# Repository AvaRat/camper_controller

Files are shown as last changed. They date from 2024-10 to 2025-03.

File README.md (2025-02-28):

# Camper Controller

## Overview
The project aims to create a usable system that can be mounted in a campervan, trailer, 4x4 overland vehicle or even small boat. It might be usefull in setups where 12V installation is present.
High level system design is presented in [system design doc](<CamperVan Control Unit system design.pdf>) .

## How to interpret this repo
Project contains electronic parts as well as control logic and user interface source codes. I decided to keep everything in one repo as all parts are pretty much dependent on each other, and with this being one-person project keeping all parts in one place make perfect sense to me.

Please see [design decisions.md](design_decisions.md) for details regarding some of the decision made.

## Roadmap
One of the gratest inspirations for me regarding how to organise things is the Opulo project: [opulo](https://github.com/opulo-inc/lumenpnp/tree/main) I'm still far away from it, but that's something I'm aiming for with respect to project structure and organisation.

Ideally I would like to use github pipelines to create BOM from PCB design files. Also somehow linking pin assignment from Kicad into C code would be great. 

Besides, the project is still in the early phase and requires some time to bring it to working prototype phase.

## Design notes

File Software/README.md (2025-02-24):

# Software for Camper Controller

UI is currently written in pure C while Control unit is done with a mix of C and C++.  This might be unified in the future.

# Overview
This part is split into [an UI part](Software/touch_screen_ui)
and [central  control unit](Software/central_control_unit).

## UI
UI is written using LVGL framework. Currently an app for 7-inch screen was done. See [an actual app](Software/touch_screen_ui/7-inch-lcd-esp32-s3/main/main.c) for more details.
Also vs-code simulator was made to allow for quick prototyping without uploading code to MCU. [a simulator](Software/touch_screen_ui/lv_port_pc_vscode)

## Central Control Unit (CCU)

Main module which will serve as a source of information to the UI. Module will communicate using CAN. This part is under heavy development currently, but some components were already done like: high-side-switch porting [hss-esp.cpp](Software/central_control_unit/components/high_side_switch/hss-esp.cpp)

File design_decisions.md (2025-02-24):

# Design Decisions

## 12V Load Switching and protection

A couple of options are available that are widely used in automotive electronics:
1. physical buttons with thermal fuses
2. relays with thermal fuses
3. semiconductor based switches with  built-in protection

My first design bas based on relays with thermal fuses. It's pretty easy to do and components are widely available. This would probably by the go-to solution for most. However after doing some research I discovered that a recent trend in automotive electronics is to utilize silicon-based switching with protection. Not only it allows to have more control but also the size of a whole device can be decreased. Additionally a module with a built in protection can be "hidden" deeply and no access for fuse replacement is required. 
I decided to try the silicon-based switching eventually. BTS700x family of switches from Infineon were used as they provide a C++ library to control them which makes a development much faster. [high-side-switch repo](https://github.com/Infineon/high-side-switch)

## MCU for Control Unit
ESP32 platform was chosen becouse of my past experience with it. I experimented with RP-Pico for some time, but with much broader, ready to use component library available for ESP-IDF platform development will be much faster. Price is comparable between those two. 

## Lightning
Initially standard 12V LED strip was planned. However with addressable LED strips like those based on WS2812b chip there are much more possibilities for amazing lightning effects, color changes and more. This is my current approach. It's realised using RMT module in ESP.

## Water Sensor
A simple sensor based on 4 metal probes is perfectly enough. This was already tested and solution based on comparator circuit (like LM393) works great.

## User Interface
Initially I wanted to do some user interface on linux OS with a SBC like RPI zero. This hovewer will increase the cost of a whole system rather significantly ($20 for a just a board without display) and the energy usage. Currently I'm exploring aa ESP32-S3 based display module like this one [crowpanel 7inch](https://www.elecrow.com/crowpanel-advance-7-0-hmi-esp32-ai-display-800x480-artificial-intelligent-ips-touch-screen-support-meshtastic-and-arduino-lvgl-micropython.ht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)
The cost for a whole module is $20-$30 which is great. Simple UI app was created for such module and you can find it here [7_inch lcd LVGL app](Software/touch_screen_ui/7-inch-lcd-esp32-s3/main/main.c)

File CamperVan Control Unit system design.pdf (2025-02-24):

# CamperVan Control Unit system design

## Introduction

While building my own van I came across multiple challenges in both domains technical and logistics. Off couse the main issue was the cost of the components that I wanted to purchase ;) That's why I started to build my own parts for it. I graduated robotics with a strong software focus, so the obvious direction for me was to develop my own control board. There are a couple of off the shelf options, but none of them suit me well.
Also designing a product from scratch that I see a specific use case for is fun.

First let's discuss market available options:
1. https://cbe.it/en/Standard-products/New-technology/Control-panels
2. https://simarine.net/via/
3. https://www.garmin.com/en-US/p/716468
4. https://www.garmin.com/en-US/p/861146/pn/010-02764-00
5. https://www.garmin.com/en-US/c/marine/digital-switching/
The rough price for such a system (central unit and display) can be between 200 and 1000 euro, so I have some room to play with.

## The main functions I want to implement and I believe are important for the end user:

1. Enable user to switch power for multiple loads
2. Provide safety for 12V power distribution system
3. Enable user to control the system from multiple places (front and rear of the van, smartphone)
4. Grid connection detection so the system can change behaviour when there's free power from the grid.
5. Provide intelligent lightning control (change of brightness, ideally color for mood-based scenarios)
6. Monitor core parameters like:
6.1. temperature outside
6.2. temperature inside
6.3. Main Battery State of Charge
6.4. Water left in main tank
6.5. Grey water tank status (if full)

Other, more generic parameters that are important:

- Ease of Use for the user
- Ease of installation
- Low price
- Small size
- Low power consumptions

## System Design

Now based on the identified requirements let’s discuss specific features and components of the system.

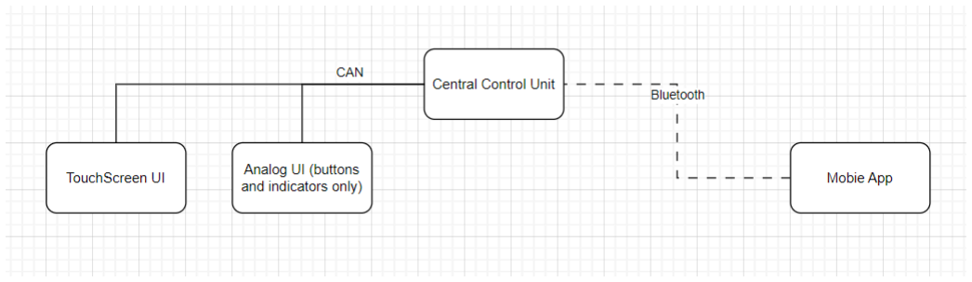
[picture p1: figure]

1. Central Control Unit

This will be the main part. All high-power connections as well as smaller loads and sensors should connect to it.This part can be mounted in inaccessible places, so another device for user interaction is required.

2. TouchScreen User Interface

Digital LCD based panel gives the most flexibility, but also requires the most work.

3. Analog User Interface

This option for user interface is the easiest to implement, so will be the cheapest. However it’s difficult to allow users to control all the features implemented in the Main Control Unit.This will be the minimal version allowing only to switch loads, display battery level and some binary indicators.

## Implementation

From the implementation perspective there are 3 parts:
1. Software:
a. Embedded development
b. User interface development
c. Mobile App (optionally)
2. Electronics:
a. Main Control Unit PCB design
b. Analog UI PCB design
c. TouchScreen module will be purchased as a ready module
3. Hardware:
a. Simple 3d-printed enclosures
b. Off the shelf buttons

This repo is split in this way too. So please check out the part that interests you the most ;)

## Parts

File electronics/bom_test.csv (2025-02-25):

Reference | Value | Datasheet | Footprint | Qty | DNP | lcsc_part | TME
C1,C3,C13,C16,C22,C23,C24,C26,C28,C29,C30,C31,C32,C33 | C_Polarized | ~ | Capacitor_THT:CP_Radial_D5.0mm_P2.50mm | 14
C2,C4,C14 | C | ~ | Capacitor_SMD:C_0805_2012Metric | 3
C5,C6,C7,C8,C15 | 1uF | ~ | Capacitor_SMD:C_0805_2012Metric | 5
C9 | 4.7uF | ~ | Capacitor_SMD:C_0805_2012Metric | 1
C10 | 22uF | ~ | Capacitor_SMD:C_0805_2012Metric | 1
C11,C12,C27 | 100nF | ~ | Capacitor_SMD:C_0805_2012Metric | 3
C17,C18,C19,C20,C21,C25 | 10uF | ~ | Capacitor_SMD:C_0805_2012Metric | 6
D1,D13,D14 | LED | ~ | LED_SMD:LED_1206_3216Metric | 3
D2 | 1N4148W | https://www.vishay.com/docs/85748/1n4148w.pdf | Diode_SMD:D_SOD-123 | 1
D3,D4,D5,D6,D7,D8,D9,D10,D11,D16,D17,D18,D19,D20,D21 | WS2812B | https://cdn-shop.adafruit.com/datasheets/WS2812B.pdf | LED_SMD:LED_WS2812B_PLCC4_5.0x5.0mm_P3.2mm | 15
D12 | D_Schottky_AKA | https://www.vishay.com/docs/98173/v6pwl45.pdf | Package_TO_SOT_SMD:TO-252-2 | 1
D15 | D_Schottky | ~ | Diode_SMD:D_SMA | 1
D22 | D_Schottky | ~ | Diode_THT:D_DO-15_P3.81mm_Vertical_AnodeUp | 1 | DNP
F1,F2,F3,F4,F5 | 20A | -- mixed values -- | HeavyDuty:ATO_fuse_holder | 5 |  | -- mixed values --
F6 | 5A | ~ | HeavyDuty:ATO_fuse_holder | 1
FB1 | FerriteBead 47 Ohm | ~ | Inductor_SMD:L_Walsin_WLFM201609x | 1
GND_Conn1,J11,U4,U12,U16,U18 | ~ |  | -- mixed values -- | 6
J1 | leds_ch1 | ~ | TerminalBlock:TerminalBlock_Xinya_XY308-2.54-3P_1x03_P2.54mm_Horizontal | 1
J2 | CAN | ~ | TerminalBlock:TerminalBlock_Xinya_XY308-2.54-2P_1x02_P2.54mm_Horizontal | 1
J3,J28 | Conn_01x08 | ~ | TerminalBlock:TerminalBlock_Xinya_XY308-2.54-8P_1x08_P2.54mm_Horizontal | 2
J4,J8,J12,J23,J24 | Conn_01x01 | ~ | HeavyDuty:keystone_m3_screw_terminal_vertical | 5
J5 | DB12 | https://www.lcsc.com/datasheet/lcsc_datasheet_2301061509_DORABO-DB128V-5-08-5P-GN-S_C2927513.pdf | HeavyDuty:5p_terminal_DB12 | 1
J6 | Inverter_Conn | ~ | HeavyDuty:keystone_m3_screw_terminal_vertical | 1
J7 | grey_water_conn | ~ | Connector_Samtec_HPM_THT:Samtec_HPM-02-01-x-S_Straight_1x02_Pitch5.08mm | 1
J9,J10 | water_sensor_conn | ~ | TerminalBlock:TerminalBlock_Xinya_XY308-2.54-5P_1x05_P2.54mm_Horizontal | 2
J13,J21,J22 | Conn_01x02 | ~ | TerminalBlock:TerminalBlock_Xinya_XY308-2.54-2P_1x02_P2.54mm_Horizontal | 3
J14,J25,J29,J30,J31 | Conn_GND | ~ | HeavyDuty:keystone_m3_screw_terminal_vertical | 5
J15 | Battery_Conn | ~ | HeavyDuty:keystone_m3_screw_terminal_vertical | 1
J16 | USB_C_Receptacle_USB2.0_16P | https://www.usb.org/sites/default/files/documents/usb_type-c.zip | Connector_USB:USB_C_Receptacle_JAE_DX07S016JA1R1500 | 1
J17,J18 | Conn_01x03 | ~ | TerminalBlock:TerminalBlock_Xinya_XY308-2.54-3P_1x03_P2.54mm_Horizontal | 2
J19 | Conn_01x03 | ~ | TerminalBlock:TerminalBlock_Xinya_XY308-2.54-3P_1x03_P2.54mm_Horizontal | 1 | DNP
J20 | leds_ch2 | ~ | TerminalBlock:TerminalBlock_Xinya_XY308-2.54-3P_1x03_P2.54mm_Horizontal | 1
J26 | leds_ch3 | ~ | TerminalBlock:TerminalBlock_Xinya_XY308-2.54-3P_1x03_P2.54mm_Horizontal | 1
J27 | leds_ch4 | ~ | TerminalBlock:TerminalBlock_Xinya_XY308-2.54-3P_1x03_P2.54mm_Horizontal | 1
Q1 | Q_NMOS_DGS | ~ | Package_TO_SOT_SMD:SOT-323_SC-70 | 1
Q2,Q3 | Q_PMOS_DGS | ~ | Package_TO_SOT_SMD:SOT-323_SC-70 | 2
Q4 | Q_NMOS_GDS | https://wmsc.lcsc.com/wmsc/upload/file/pdf/v2/lcsc/2310271812_UMW-Youtai-Semiconductor-Co---Ltd--AOD413A-UMW_C19100585.pdf | Package_TO_SOT_SMD:TO-252-2 | 1
R1,R27,R32,R37,R38,R39 | 10k | ~ | Resistor_SMD:R_0805_2012Metric | 6
R2,R36 | 100R | ~ | Resistor_SMD:R_0805_2012Metric | 2
R3,R4,R18,R19,R20,R33,R34,R35 | 4k7 | ~ | Resistor_SMD:R_0805_2012Metric | 8
R5,R8 | 0.001 Ohm 10W | https://www.mouser.pl/datasheet/2/392/Susumu_7_1_2024_MSRSF-3471975.pdf | HeavyDuty:MSRSF_shunt_resistor | 2
R6 | 0.003 Ohm 10W | https://www.mouser.pl/ProductDetail/Susumu/MSRSF5930P-3L00-F2P0?qs=VVKQmw408U%252Bnsh6uhhzxQg%3D%3D | HeavyDuty:MSRSF_shunt_resistor | 1
R7,R9,R10,R11,R12,R13 | 10 ohm | -- mixed values -- | Resistor_SMD:R_0805_2012Metric | 6
R14,R15,R21,R_DEN1,R_DEN2,R_DEN3,R_DEN4,R_DEN5,R_IN1,R_IN2,R_IN3,R_IN4,R_IN5 | 4.7k | -- mixed values -- | Resistor_SMD:R_0805_2012Metric | 13
R16,R23,R24,R26 | 100k | -- mixed values -- | -- mixed values -- | 4
R17 | 120 | ~ | Resistor_SMD:R_0805_2012Metric | 1
R22 | 50 Ohm | ~ | Resistor_SMD:R_0805_2012Metric | 1
R25 | 4.7kΩ | ~ | Resistor_SMD:R_0805_2012Metric | 1
R28,R29,R30,R31 | 1M | ~ | Resistor_SMD:R_0805_2012Metric | 4
RL1 | AZSR131-1AE-12D | https://www.mouser.pl/datasheet/2/1628/pre29-3510988.pdf | HeavyDuty:PRE29-same-sky | 1
SW1,SW2,SW3,SW4,SW5 | SW_Push | ~ | analog_ui:button_12mm | 5
SW6 | SW_DIP_x01 | ~ | Connector_PinHeader_1.00mm:PinHeader_1x02_P1.00mm_Vertical | 1
SW7 | RST_BTN | ~ | Button_Switch_THT:SW_PUSH_6mm_H4.3mm | 1
SW8 | FLASH_BTN | ~ | Button_Switch_THT:SW_PUSH_6mm_H4.3mm | 1
U1 | TLV1117-33 | http://www.ti.com/lit/ds/symlink/tlv1117.pdf | Package_TO_SOT_SMD:SOT-223-3_TabPin2 | 1
U3 | TJA1051T-3 | http://www.nxp.com/docs/en/data-sheet/TJA1051.pdf | Package_SO:SOIC-8_3.9x4.9mm_P1.27mm | 1
U5,U14 | LM339_4ch |  | Package_SO:SOIC-14_3.9x8.7mm_P1.27mm | 2
U6,U7,U8,U9,U10 | BTS7006 | https://www.infineon.com/dgdl/Infineon-BTS7004-1EPP-DS-v01_00-EN.pdf?fileId=5546d4626102d35a016147550a725555 | Package_SO:Infineon_PG-TSDSO-14-22 | 5
U11 | INA3221 | http://www.ti.com/lit/ds/symlink/ina3221.pdf | Package_DFN_QFN:Texas_RGV0016A_VQFN-16-1EP_4x4mm_P0.65mm_EP2.1x2.1mm | 1
U13 | CNY17-1 | http://www.vishay.com/docs/83606/cny17.pdf | Package_TO_SOT_SMD:SOT-23-6 | 1
U15 | TCA9555PWR | http://www.ti.com/lit/ds/symlink/tca9555.pdf | Package_SO:TSSOP-24_4.4x7.8mm_P0.65mm | 1 |  |  | TCA9554APWR
U17 | H11AA1 | https://www.vishay.com/docs/83608/h11aa1.pdf | Package_DIP:DIP-6_W7.62mm | 1
U19 | ESP32-S3-MINI-1 | https://www.espressif.com/sites/default/files/documentation/esp32-s3-mini-1_mini-1u_datasheet_en.pdf | PCM_Espressif:ESP32-S3-MINI-1U | 1

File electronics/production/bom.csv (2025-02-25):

Designator | Footprint | Quantity | Value | LCSC Part #
C1, C13, C16, C22, C23, C24, C26, C28, C29, C3, C30, C31, C32, C33 | CP_Radial_D5.0mm_P2.50mm | 14 | C_Polarized
C10_2, C10 | 0805 | 2 | 22uF
C11, C12, C27 | 0805 | 3 | 100nF
C14, C2, C4 | 0805 | 3 | C
C15, C5, C6, C7, C8 | 0805 | 5 | 1uF
C17, C18, C19, C20, C21, C25 | 0805 | 6 | 10uF
C9 | 0805 | 1 | 4.7uF
D1, D13, D14 | 1206 | 3 | LED
D10, D11, D16, D17, D18, D19, D20, D21, D3, D4, D5, D6, D7, D8, D9 | LED_WS2812B_PLCC4_5.0x5.0mm_P3.2mm | 15 | WS2812B
D12 | TO-252-2 | 1 | D_Schottky_AKA
D15 | D_SMA | 1 | D_Schottky
D2 | D_SOD-123 | 1 | 1N4148W
D22 | D_DO-15_P3.81mm_Vertical_AnodeUp | 1 | D_Schottky
F1, F2, F3, F4, F5 | ATO_fuse_holder | 5 | 20A
F6 | ATO_fuse_holder | 1 | 5A
FB1 | L_Walsin_WLFM201609x | 1 | FerriteBead 47 Ohm
GND_CONN1 | small_busbar-15mm | 1 | ~
J1 | TerminalBlock_Xinya_XY308-2.54-3P_1x03_P2.54mm_Horizontal | 1 | leds_ch1
J10, J9 | TerminalBlock_Xinya_XY308-2.54-5P_1x05_P2.54mm_Horizontal | 2 | water_sensor_conn
J11 | water_sensor_rods | 1 | ~
J12, J23, J24, J4, J8 | keystone_m3_screw_terminal_vertical | 5 | Conn_01x01
J13, J21, J22 | TerminalBlock_Xinya_XY308-2.54-2P_1x02_P2.54mm_Horizontal | 3 | Conn_01x02
J14, J25, J29, J30, J31 | keystone_m3_screw_terminal_vertical | 5 | Conn_GND
J15 | keystone_m3_screw_terminal_vertical | 1 | Battery_Conn
J16 | USB_C_Receptacle_JAE_DX07S016JA1R1500 | 1 | USB_C_Receptacle_USB2.0_16P
J17, J18 | TerminalBlock_Xinya_XY308-2.54-3P_1x03_P2.54mm_Horizontal | 2 | Conn_01x03
J2 | TerminalBlock_Xinya_XY308-2.54-2P_1x02_P2.54mm_Horizontal | 1 | CAN
J20 | TerminalBlock_Xinya_XY308-2.54-3P_1x03_P2.54mm_Horizontal | 1 | leds_ch2
J26 | TerminalBlock_Xinya_XY308-2.54-3P_1x03_P2.54mm_Horizontal | 1 | leds_ch3
J27 | TerminalBlock_Xinya_XY308-2.54-3P_1x03_P2.54mm_Horizontal | 1 | leds_ch4
J28, J3 | TerminalBlock_Xinya_XY308-2.54-8P_1x08_P2.54mm_Horizontal | 2 | Conn_01x08
J5 | 5p_terminal_DB12 | 1 | DB12
J6 | keystone_m3_screw_terminal_vertical | 1 | Inverter_Conn
J7 | Samtec_HPM-02-01-x-S_Straight_1x02_Pitch5.08mm | 1 | grey_water_conn
Q1 | SOT-323_SC-70 | 1 | Q_NMOS_DGS
Q2, Q3 | SOT-323_SC-70 | 2 | Q_PMOS_DGS
Q4 | TO-252-2 | 1 | Q_NMOS_GDS | C19100585
R1, R27, R32, R37, R38, R39 | 0805 | 6 | 10k
R10, R11, R12, R13, R7, R9 | 0805 | 6 | 10 ohm
R14, R15, R21, R_DEN1, R_DEN2, R_DEN3, R_DEN4, R_DEN5, R_IN1, R_IN2, R_IN3, R_IN4, R_IN5 | 0805 | 13 | 4.7k
R16, R26 | 0805 | 2 | 100k
R17 | 0805 | 1 | 120
R18, R19, R20, R3, R33, R34, R35, R4 | 0805 | 8 | 4k7
R2, R36 | 0805 | 2 | 100R
R22 | 0805 | 1 | 50 Ohm
R23, R24 | R_Axial_DIN0207_L6.3mm_D2.5mm_P7.62mm_Horizontal | 2 | 100k
R25 | 0805 | 1 | 4.7kΩ
R28, R29, R30, R31 | 0805 | 4 | 1M
R5, R8 | MSRSF_shunt_resistor | 2 | 0.001 Ohm 10W
R6 | MSRSF_shunt_resistor | 1 | 0.003 Ohm 10W
RL1 | PRE29-same-sky | 1 | AZSR131-1AE-12D
SW1, SW2, SW3, SW4, SW5 | button_12mm | 5 | SW_Push
SW6 | PinHeader_1x02_P1.00mm_Vertical | 1 | SW_DIP_x01
SW7 | SW_PUSH_6mm_H4.3mm | 1 | RST_BTN
SW8 | SW_PUSH_6mm_H4.3mm | 1 | FLASH_BTN
U1 | SOT-223-3_TabPin2 | 1 | TLV1117-33 | C37359
U10, U7, U8, U9 | Infineon_PG-TSDSO-14-22 | 4 | BTS7006
U11 | Texas_RGV0016A_VQFN-16-1EP_4x4mm_P0.65mm_EP2.1x2.1mm | 1 | INA3221
U12 | 2_water_sensor_rods | 1 | ~
U13 | SOT-23-6 | 1 | CNY17-1
U14, U5 | SOIC-14_3.9x8.7mm_P1.27mm | 2 | LM339_4ch | C7948
U15 | TSSOP-24_4.4x7.8mm_P0.65mm | 1 | TCA9555PWR | C465732
U16, U4 | generic_dcdc | 2 | ~
U17 | DIP-6_W7.62mm | 1 | H11AA1
U18 | mini360 | 1 | ~
U19 | ESP32-S3-MINI-1U | 1 | ESP32-S3-MINI-1
U3 | SOIC-8_3.9x4.9mm_P1.27mm | 1 | TJA1051T-3
U6 | Infineon_PG-TSDSO-14-22 | 1 | BTS7006

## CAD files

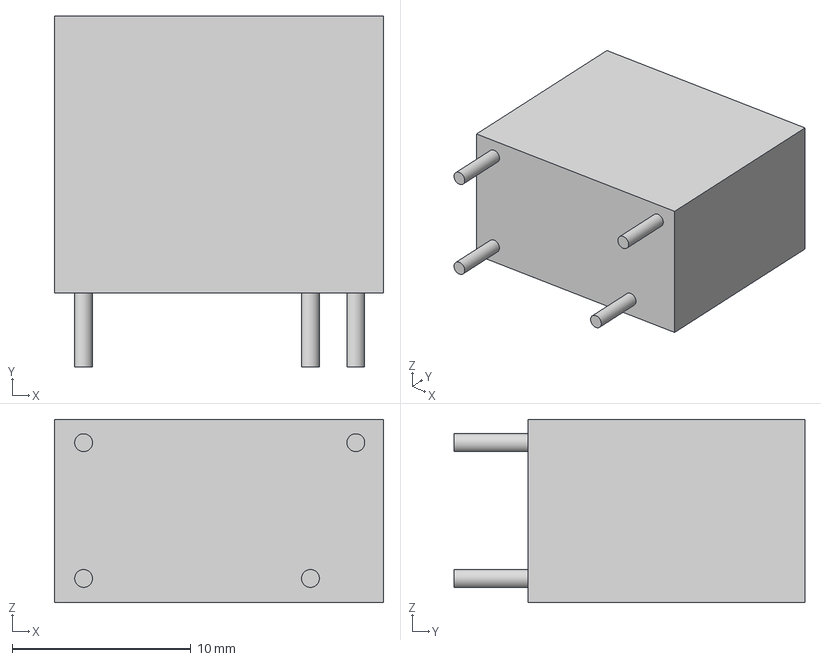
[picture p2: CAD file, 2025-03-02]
electronics/3d_models/PRE-29-same-sky-relay.step
18.4 x 19.6 x 10.2 mm

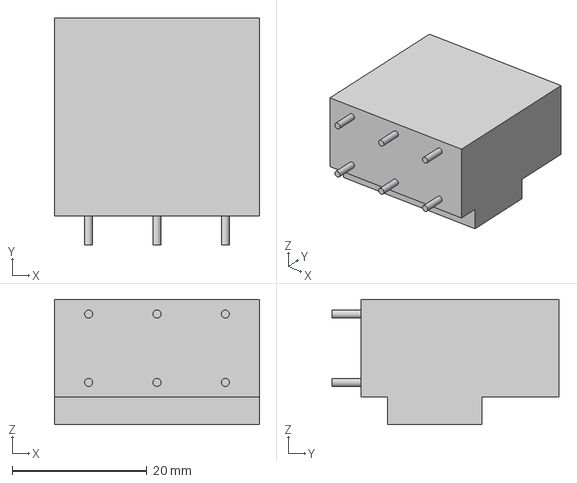
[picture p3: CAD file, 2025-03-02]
electronics/3d_models/3p-10-conn v2.step
30.5 x 33.8 x 18.6 mm

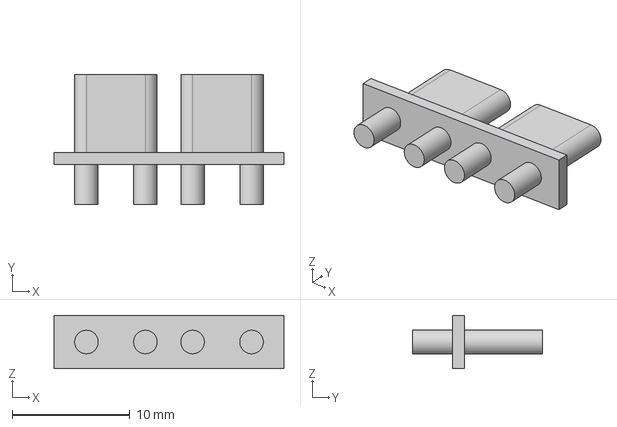
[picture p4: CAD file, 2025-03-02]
electronics/3d_models/ATO-fuse-holder v0.step
19.5 x 11.0 x 4.50 mm

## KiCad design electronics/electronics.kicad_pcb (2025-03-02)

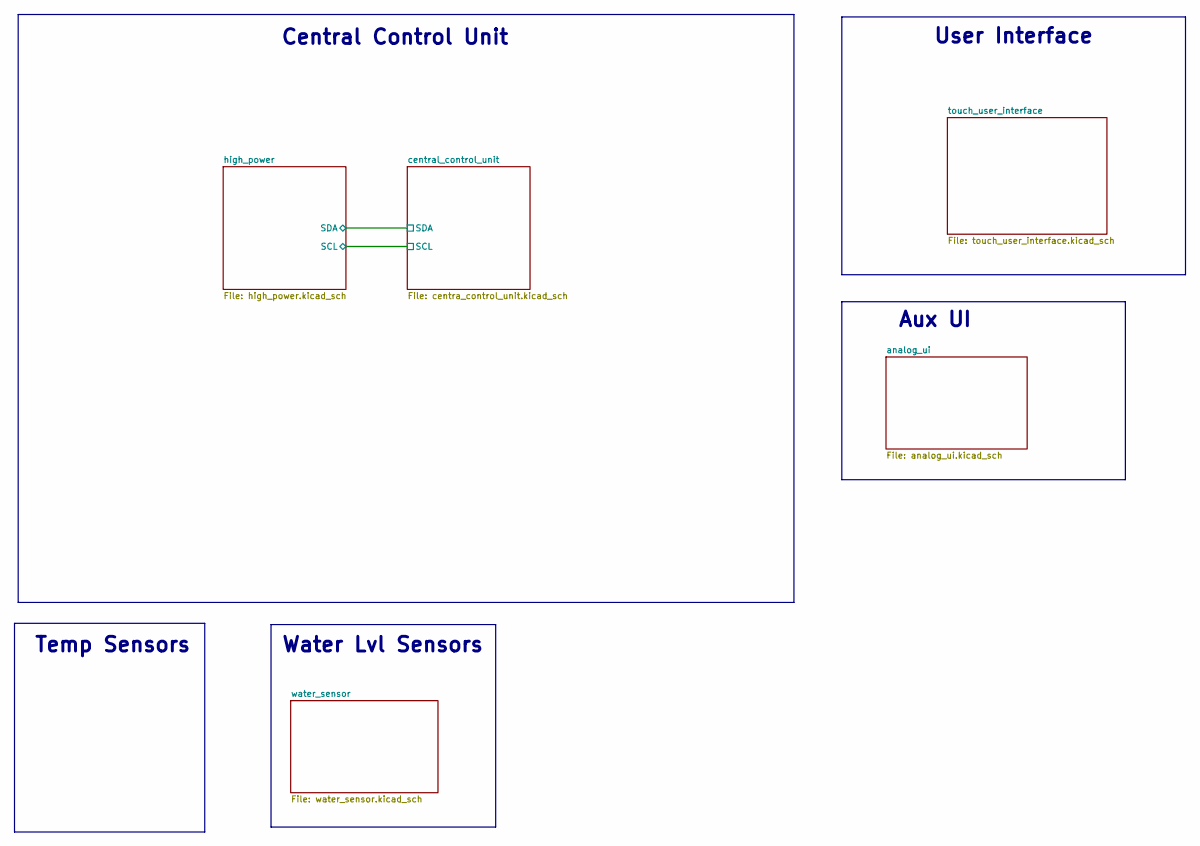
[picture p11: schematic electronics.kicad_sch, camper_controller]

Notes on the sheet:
User Interface
Central Control Unit
Temp Sensors
Water Lvl Sensors
Aux UI

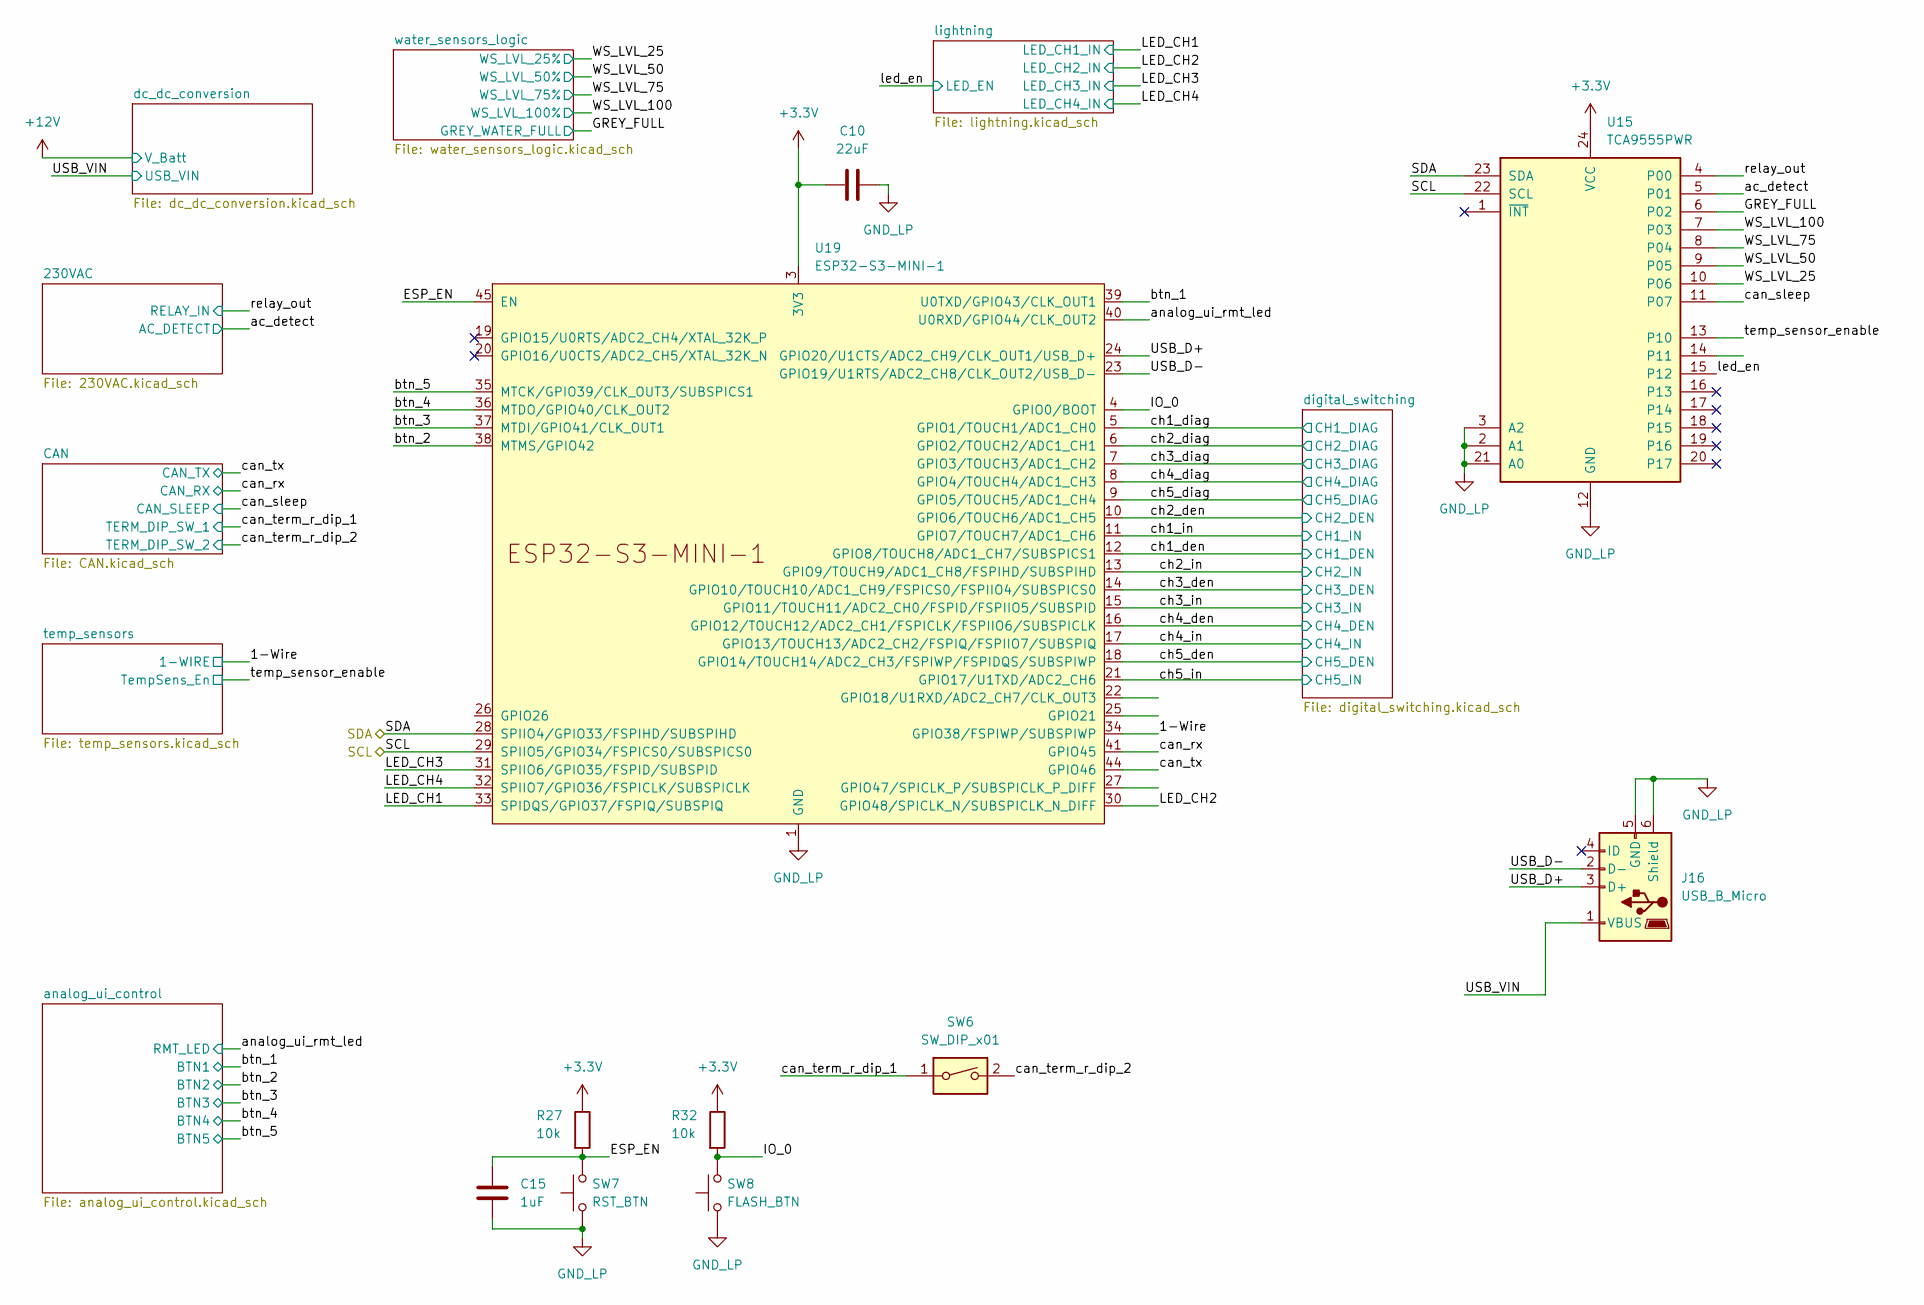
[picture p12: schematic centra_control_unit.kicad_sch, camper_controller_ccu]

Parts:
C10: 22uF; C_0805_2012Metric
C15: 1uF; C_0805_2012Metric
J16: USB_B_Micro; USB_Micro-B_Wuerth_614105150721_Vertical; LCSC C2926997
R27, R32: 10k; R_0805_2012Metric
SW6: SW_DIP_x01; PinHeader_1x02_P1.00mm_Vertical
SW7: RST_BTN; SW_PUSH_6mm_H4.3mm
SW8: FLASH_BTN; SW_PUSH_6mm_H4.3mm
U15: TCA9555PWR; TSSOP-24_4.4x7.8mm_P0.65mm; LCSC C465732
U19: ESP32-S3-MINI-1; ESP32-S3-MINI-1U

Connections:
+3.3V: C10.2, R27.1, R32.1, U15.24 (VCC), U19.3 (3V3); also elsewhere on the board
/central_control_unit/1-Wire: U19.34 (GPIO38/FSPIWP/SUBSPIWP); also elsewhere on the board
/central_control_unit/ESP_EN: C15.1, R27.2, SW7.2, U19.45 (EN)
/central_control_unit/GREY_FULL: U15.6 (P02); also elsewhere on the board
/central_control_unit/IO_0: R32.2, SW8.2, U19.4 (GPIO0/BOOT)
/central_control_unit/LED_CH1: U19.33 (SPIDQS/GPIO37/FSPIQ/SUBSPIQ); also elsewhere on the board
/central_control_unit/LED_CH2: U19.30 (GPIO48/SPICLK_N/SUBSPICLK_N_DIFF); also elsewhere on the board
/central_control_unit/LED_CH3: U19.31 (SPIIO6/GPIO35/FSPID/SUBSPID); also elsewhere on the board
/central_control_unit/LED_CH4: U19.32 (SPIIO7/GPIO36/FSPICLK/SUBSPICLK); also elsewhere on the board
/central_control_unit/SCL: U15.22 (SCL), U19.29 (SPIIO5/GPIO34/FSPICS0/SUBSPICS0); also elsewhere on the board
/central_control_unit/SDA: U15.23 (SDA), U19.28 (SPIIO4/GPIO33/FSPIHD/SUBSPIHD); also elsewhere on the board
/central_control_unit/USB_D+: J16.3 (D+), U19.24 (GPIO20/U1CTS/ADC2_CH9/CLK_OUT1/USB_D+)
/central_control_unit/USB_D-: J16.2 (D-), U19.23 (GPIO19/U1RTS/ADC2_CH8/CLK_OUT2/USB_D-)
/central_control_unit/USB_VIN: J16.1 (VBUS); also elsewhere on the board
/central_control_unit/WS_LVL_25: U15.10 (P06); also elsewhere on the board
/central_control_unit/WS_LVL_50: U15.9 (P05); also elsewhere on the board
/central_control_unit/WS_LVL_75: U15.8 (P04); also elsewhere on the board
/central_control_unit/WS_LVL_100: U15.7 (P03); also elsewhere on the board
/central_control_unit/ac_detect: U15.5 (P01); also elsewhere on the board
/central_control_unit/analog_ui_rmt_led: U19.40 (U0RXD/GPIO44/CLK_OUT2); also elsewhere on the board
/central_control_unit/btn_1: U19.39 (U0TXD/GPIO43/CLK_OUT1); also elsewhere on the board
/central_control_unit/btn_2: U19.38 (MTMS/GPIO42); also elsewhere on the board
/central_control_unit/btn_3: U19.37 (MTDI/GPIO41/CLK_OUT1); also elsewhere on the board
/central_control_unit/btn_4: U19.36 (MTDO/GPIO40/CLK_OUT2); also elsewhere on the board
/central_control_unit/btn_5: U19.35 (MTCK/GPIO39/CLK_OUT3/SUBSPICS1); also elsewhere on the board
/central_control_unit/can_rx: U19.41 (GPIO45); also elsewhere on the board
/central_control_unit/can_sleep: U15.11 (P07); also elsewhere on the board
/central_control_unit/can_term_r_dip_1: SW6.1; also elsewhere on the board
/central_control_unit/can_term_r_dip_2: SW6.2; also elsewhere on the board
/central_control_unit/can_tx: U19.44 (GPIO46); also elsewhere on the board
/central_control_unit/ch1_den: U19.12 (GPIO8/TOUCH8/ADC1_CH7/SUBSPICS1); also elsewhere on the board
/central_control_unit/ch1_diag: U19.5 (GPIO1/TOUCH1/ADC1_CH0); also elsewhere on the board
/central_control_unit/ch1_in: U19.11 (GPIO7/TOUCH7/ADC1_CH6); also elsewhere on the board
/central_control_unit/ch2_den: U19.10 (GPIO6/TOUCH6/ADC1_CH5); also elsewhere on the board
/central_control_unit/ch2_diag: U19.6 (GPIO2/TOUCH2/ADC1_CH1); also elsewhere on the board
/central_control_unit/ch2_in: U19.13 (GPIO9/TOUCH9/ADC1_CH8/FSPIHD/SUBSPIHD); also elsewhere on the board
/central_control_unit/ch3_den: U19.14 (GPIO10/TOUCH10/ADC1_CH9/FSPICS0/FSPIIO4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); also elsewhere on the board
/central_control_unit/ch3_diag: U19.7 (GPIO3/TOUCH3/ADC1_CH2); also elsewhere on the board
/central_control_unit/ch3_in: U19.15 (GPIO11/TOUCH11/ADC2_CH0/FSPID/FSPIIO5/S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); also elsewhere on the board
/central_control_unit/ch4_den: U19.16 (GPIO12/TOUCH12/ADC2_CH1/FSPICLK/FSPIIO6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); also elsewhere on the board
/central_control_unit/ch4_diag: U19.8 (GPIO4/TOUCH4/ADC1_CH3); also elsewhere on the board
/central_control_unit/ch4_in: U19.17 (GPIO13/TOUCH13/ADC2_CH2/FSPIQ/FSPIIO7/S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); also elsewhere on the board
/central_control_unit/ch5_den: U19.18 (GPIO14/TOUCH14/ADC2_CH3/FSPIWP/FSPIDQS/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); also elsewhere on the board
/central_control_unit/ch5_diag: U19.9 (GPIO5/TOUCH5/ADC1_CH4); also elsewhere on the board
/central_control_unit/digital_switching/CH5_IN: U19.21 (GPIO17/U1TXD/ADC2_CH6); also elsewhere on the board
/central_control_unit/led_en: U15.15 (P12); also elsewhere on the board
/central_control_unit/relay_out: U15.4 (P00); also elsewhere on the board
/central_control_unit/temp_sensor_enable: U15.13 (P10); also elsewhere on the board
GND_LP: C10.1, C15.2, J16.5 (GND), J16.6 (Shield), SW7.1, SW8.1, U15.2 (A1), U15.3 (A2), U15.12 (GND), U15.21 (A0), U19.1 (GND), U19.2 (GND), U19.42 (GND), U19.43 (GND), U19.46 (GND), U19.47 (GND), U19.48 (GND), U19.49 (GND), U19.50 (GND), U19.51 (GND), U19.52 (GND), U19.53 (GND), U19.54 (GND), U19.55 (GND), U19.56 (GND), U19.57 (GND), U19.58 (GND), U19.59 (GND), U19.60 (GND), U19.61 (GND), U19.62 (GND), U19.63 (GND), U19.64 (GND), U19.65 (GND); also elsewhere on the board

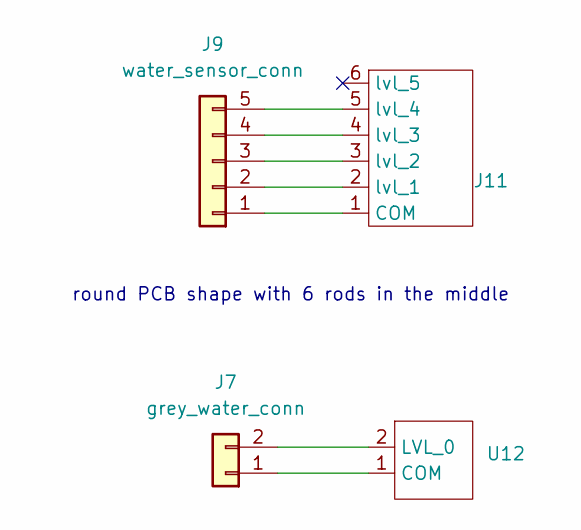
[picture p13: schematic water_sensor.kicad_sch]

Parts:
J7: grey_water_conn; Samtec_HPM-02-01-x-S_Straight_1x02_Pitch5.08mm
J9: water_sensor_conn; TerminalBlock_Xinya_XY308-2.54-5P_1x05_P2.54mm_Horizontal
J11: water_sensor_rods
U12: 2_water_sensor_rods

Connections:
unnamed: J7.1, U12.1 (COM)
unnamed: J7.2, U12.2 (LVL_0)
unnamed: J9.1, J11.1 (COM)
unnamed: J9.2, J11.2 (lvl_1)
unnamed: J9.3, J11.3 (lvl_2)
unnamed: J9.4, J11.4 (lvl_3)
unnamed: J9.5, J11.5 (lvl_4)

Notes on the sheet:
round PCB shape with 6 rods in the middle

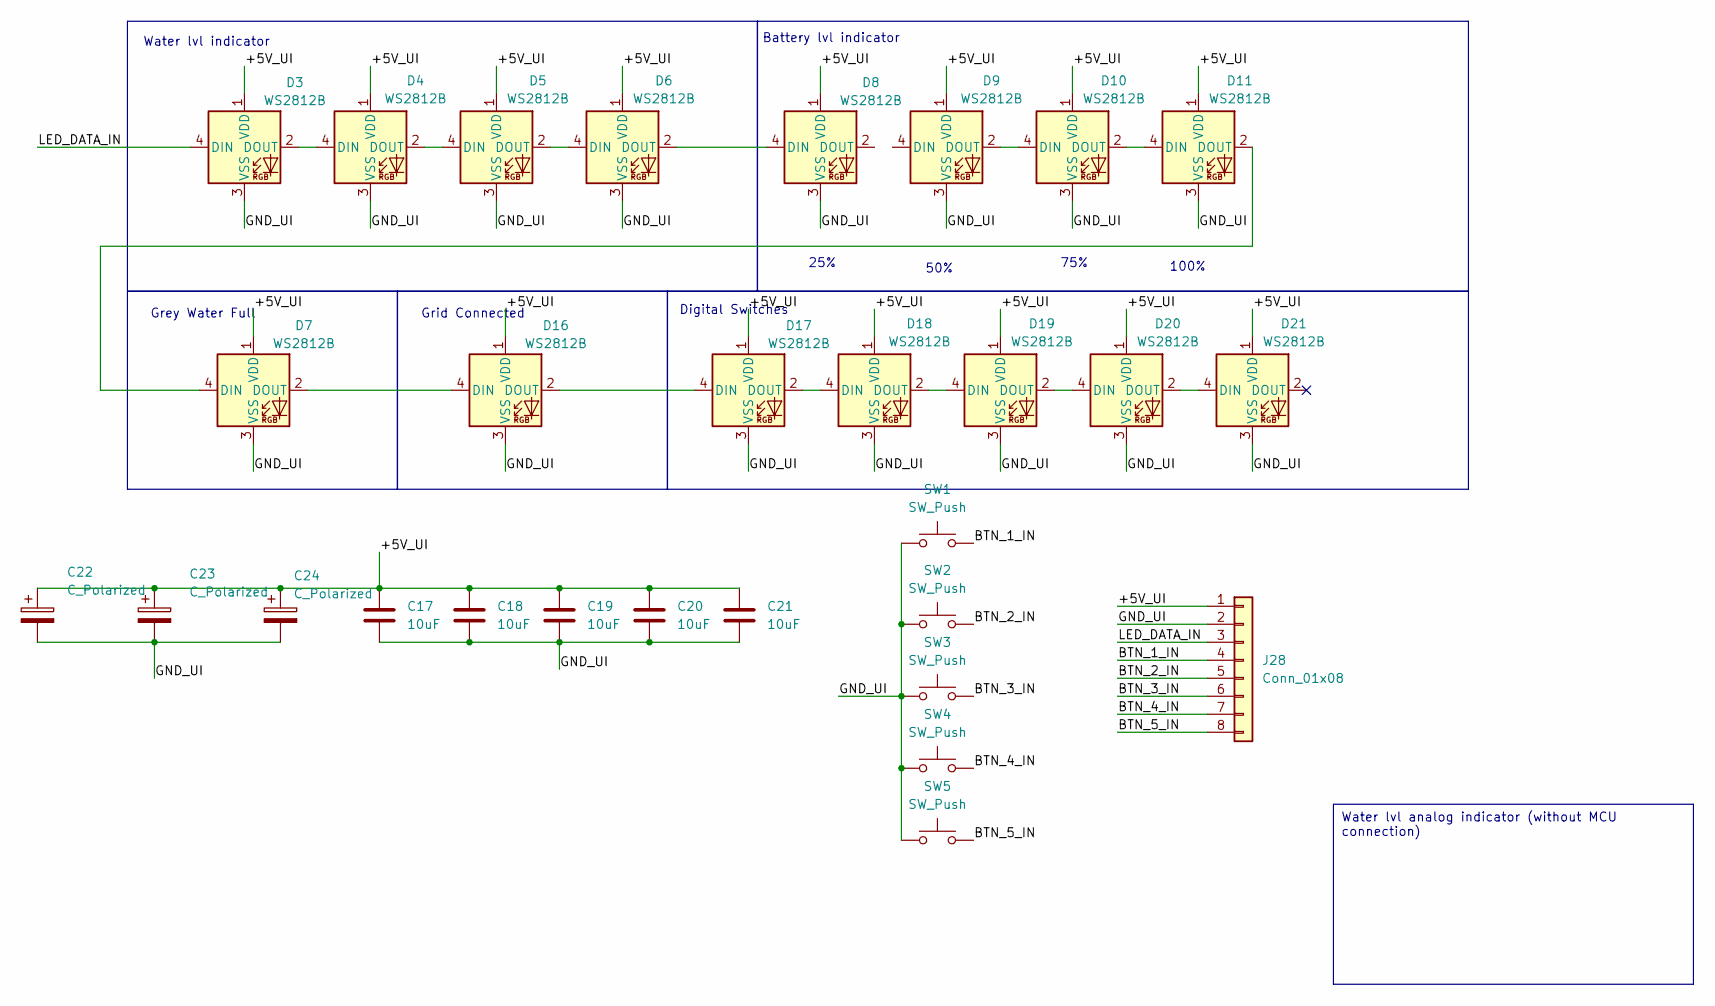
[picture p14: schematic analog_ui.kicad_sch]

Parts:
C17, C18, C19, C20, C21: 10uF; C_0805_2012Metric
C22, C23, C24: C_Polarized; CP_Radial_D5.0mm_P2.50mm
D3, D4, D5, D6, D7, D8, D9, D10, D11, D16, D17, D18, D19, D20, D21: WS2812B; LED_WS2812B_PLCC4_5.0x5.0mm_P3.2mm
J28: Conn_01x08; TerminalBlock_Xinya_XY308-2.54-8P_1x08_P2.54mm_Horizontal
SW1, SW2, SW3, SW4, SW5: SW_Push; button_12mm

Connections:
/analog_ui/+5V_UI: C17.1, C18.1, C19.1, C20.1, C21.1, C22.1, C23.1, C24.1, D3.1 (VDD), D4.1 (VDD), D5.1 (VDD), D6.1 (VDD), D7.1 (VDD), D8.1 (VDD), D9.1 (VDD), D10.1 (VDD), D11.1 (VDD), D16.1 (VDD), D17.1 (VDD), D18.1 (VDD), D19.1 (VDD), D20.1 (VDD), D21.1 (VDD), J28.1
/analog_ui/BTN_1_IN: J28.4, SW1.2
/analog_ui/BTN_2_IN: J28.5, SW2.2
/analog_ui/BTN_3_IN: J28.6, SW3.2
/analog_ui/BTN_4_IN: J28.7, SW4.2
/analog_ui/BTN_5_IN: J28.8, SW5.2
/analog_ui/GND_UI: C17.2, C18.2, C19.2, C20.2, C21.2, C22.2, C23.2, C24.2, D3.3 (VSS), D4.3 (VSS), D5.3 (VSS), D6.3 (VSS), D7.3 (VSS), D8.3 (VSS), D9.3 (VSS), D10.3 (VSS), D11.3 (VSS), D16.3 (VSS), D17.3 (VSS), D18.3 (VSS), D19.3 (VSS), D20.3 (VSS), D21.3 (VSS), J28.2, SW1.1, SW2.1, SW3.1, SW4.1, SW5.1
/analog_ui/LED_DATA_IN: D3.4 (DIN), J28.3
unnamed: D3.2 (DOUT), D4.4 (DIN)
unnamed: D4.2 (DOUT), D5.4 (DIN)
unnamed: D5.2 (DOUT), D6.4 (DIN)
unnamed: D6.2 (DOUT), D8.4 (DIN)
unnamed: D9.2 (DOUT), D10.4 (DIN)
unnamed: D10.2 (DOUT), D11.4 (DIN)
unnamed: D7.4 (DIN), D11.2 (DOUT)
unnamed: D7.2 (DOUT), D16.4 (DIN)
unnamed: D16.2 (DOUT), D17.4 (DIN)
unnamed: D17.2 (DOUT), D18.4 (DIN)
unnamed: D18.2 (DOUT), D19.4 (DIN)
unnamed: D19.2 (DOUT), D20.4 (DIN)
unnamed: D20.2 (DOUT), D21.4 (DIN)

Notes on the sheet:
Water lvl analog indicator (without MCU connection)
Grid Connected
75%
Water lvl indicator
Battery lvl indicator
25%
50%
Grey Water Full
Digital Switches
100%

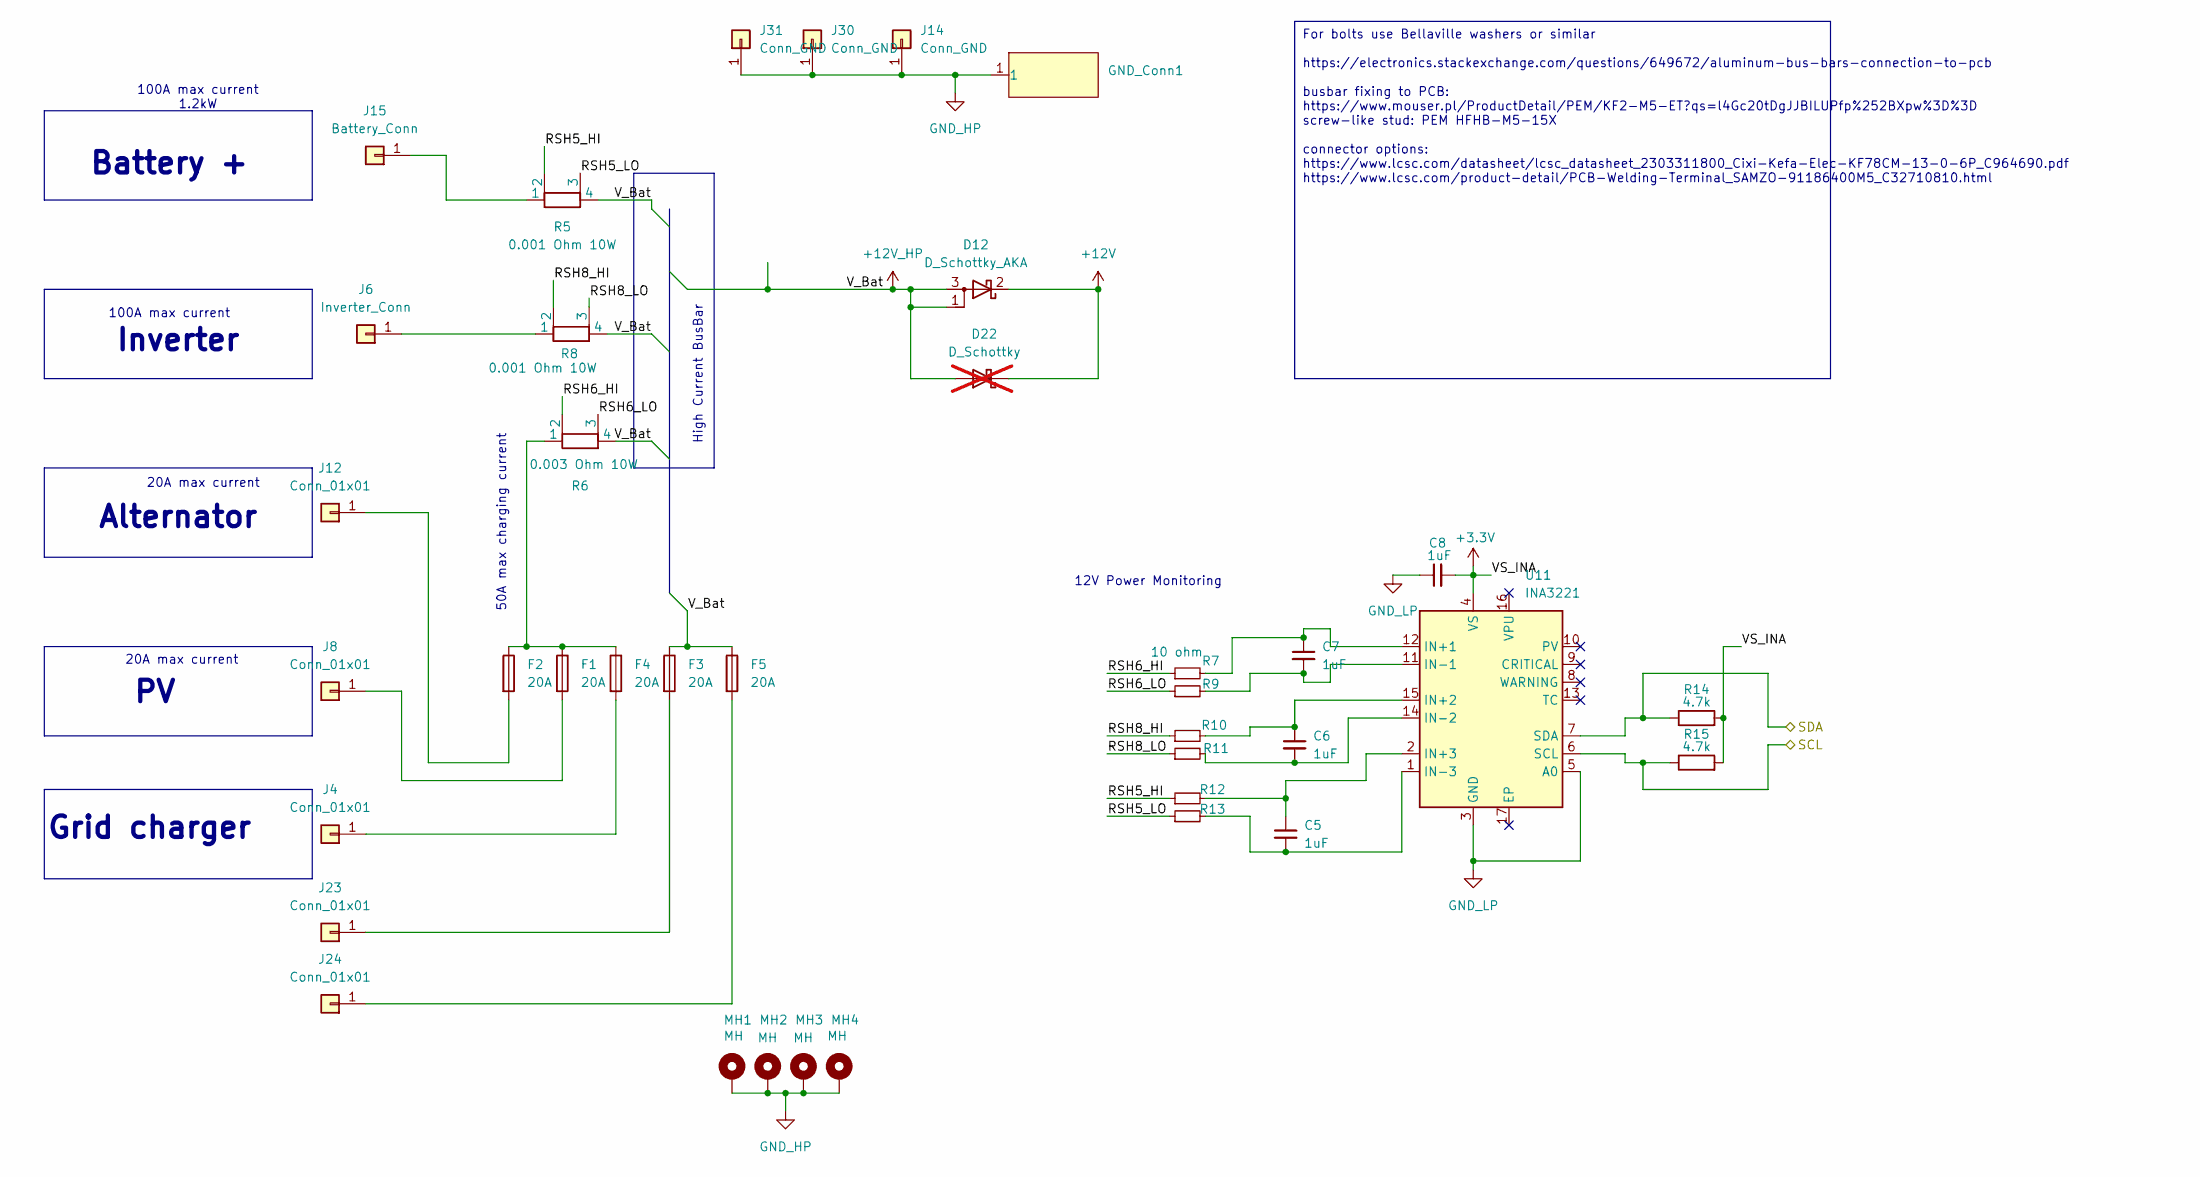
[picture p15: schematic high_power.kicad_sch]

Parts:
C5, C6, C7, C8: 1uF; C_0805_2012Metric
D12: D_Schottky_AKA; TO-252-2
D22: D_Schottky; D_DO-15_P3.81mm_Vertical_AnodeUp; not fitted
F1, F3, F5: 20A; ATO_fuse_holder; LCSC_part C2935871
F2: 20A; ATO_fuse_holder
F4: 20A; ATO_fuse_holder; lcsc_part C2935871
GND_Conn1: small_busbar-15mm
J4, J8, J12, J23, J24: Conn_01x01; keystone_m3_screw_terminal_vertical
J6: Inverter_Conn; keystone_m3_screw_terminal_vertical
J14, J30, J31: Conn_GND; keystone_m3_screw_terminal_vertical
J15: Battery_Conn; keystone_m3_screw_terminal_vertical
MH1, MH2, MH3, MH4: MH; MountingHole_3.2mm_M3_ISO7380_Pad_TopBottom
R5, R8: 0.001 Ohm 10W; MSRSF_shunt_resistor; Mouser_Nr 754-MSRSF5930P1L0F2P
R6: 0.003 Ohm 10W; MSRSF_shunt_resistor; Mouser_Nr 754-MSRSF5930P1L0F2P
R7, R9, R10, R11, R12, R13: 10 ohm; R_0805_2012Metric
R14, R15: 4.7k; R_0805_2012Metric
U11: INA3221; Texas_RGV0016A_VQFN-16-1EP_4x4mm_P0.65mm_EP2.1x2.1mm

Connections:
+3.3V: C8.2, R14.2, R15.2, U11.4 (VS); also elsewhere on the board
+12V: D12.2 (K), D22.1 (K); also elsewhere on the board
+12V_HP: D12.1 (A), D12.3 (A), D22.2 (A), F3.1, F5.1, R5.4, R6.4, R8.4; also elsewhere on the board
/central_control_unit/SCL: R15.1, U11.6 (SCL); also elsewhere on the board
/central_control_unit/SDA: R14.1, U11.7 (SDA); also elsewhere on the board
/high_power/RSH5_HI: R5.2, R12.1
/high_power/RSH5_LO: R5.3, R13.1
/high_power/RSH6_HI: R6.2, R7.1
/high_power/RSH6_LO: R6.3, R9.1
/high_power/RSH8_HI: R8.2, R10.1
/high_power/RSH8_LO: R8.3, R11.1
GND_HP: GND_Conn1.1, J14.1, J30.1, J31.1, MH1.1, MH2.1, MH3.1, MH4.1; also elsewhere on the board
GND_LP: C8.1, U11.3 (GND), U11.5 (A0); also elsewhere on the board
unnamed: F1.1, F2.1, F4.1, R6.1
unnamed: F4.2, J4.1
unnamed: J6.1, R8.1
unnamed: F1.2, J8.1
unnamed: F2.2, J12.1
unnamed: J15.1, R5.1
unnamed: F3.2, J23.1
unnamed: F5.2, J24.1
unnamed: C7.1, R7.2, U11.12 (IN+1)
unnamed: C6.1, R10.2, U11.15 (IN+2)
unnamed: C5.1, R12.2, U11.2 (IN+3)
unnamed: C7.2, R9.2, U11.11 (IN-1)
unnamed: C6.2, R11.2, U11.14 (IN-2)
unnamed: C5.2, R13.2, U11.1 (IN-3)

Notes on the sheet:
For bolts use Bellaville washers or similar https://electronics.stackexchange.com/questions/649672/aluminum-bus-bars-connection-to-pcb busbar fixing to PCB: https://www.mouser.pl/ProductDetail/PEM/KF2-M5-ET?qs=l4Gc20tDgJJBILUPfp%252BXpw%3D%3D screw-like stud: PEM HFHB-M5-15X connector options: http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
100A max current
50A max charging current
100A max current 1.2kW
Inverter
Battery +
20A max current
Alternator
12V Power Monitoring
Grid charger
High Current BusBar

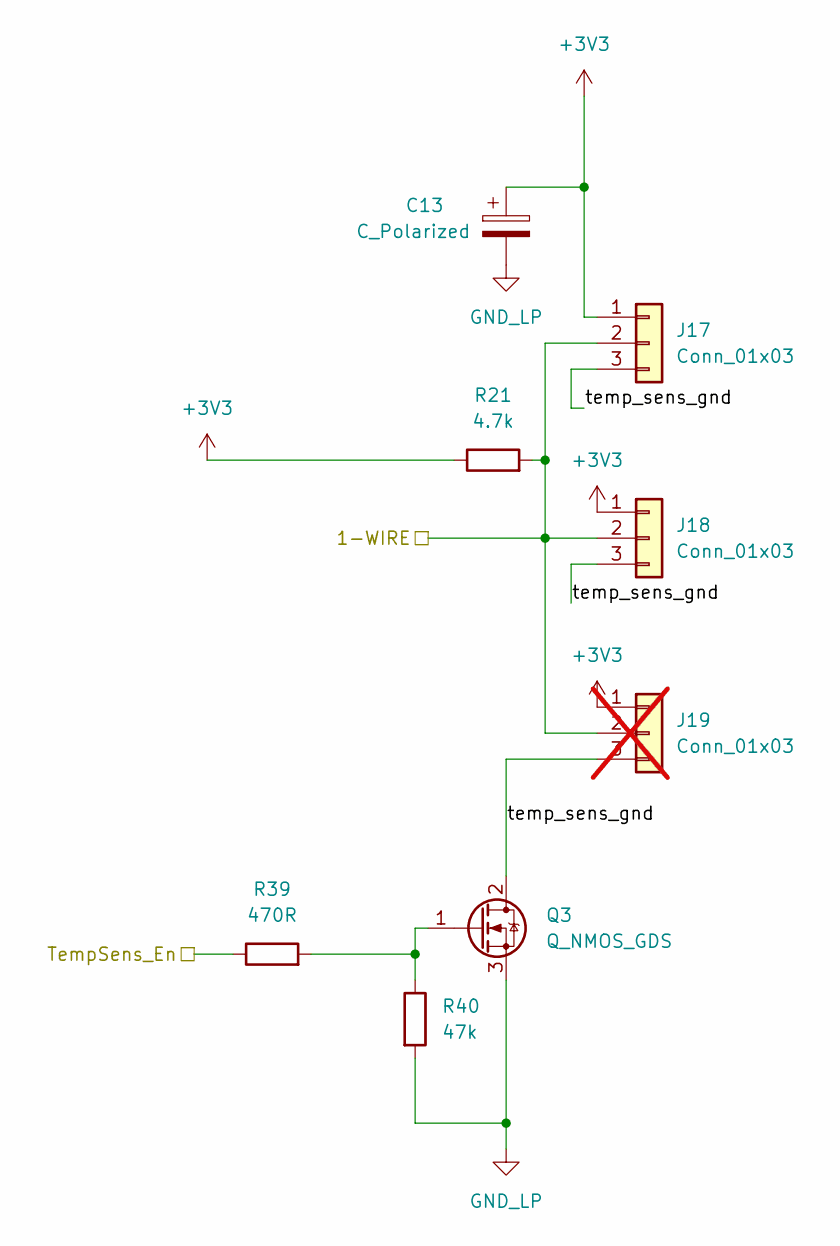
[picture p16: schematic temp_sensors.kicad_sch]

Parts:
C13: C_Polarized; CP_Radial_D5.0mm_P2.50mm
J17, J18: Conn_01x03; TerminalBlock_Xinya_XY308-2.54-3P_1x03_P2.54mm_Horizontal
J19: Conn_01x03; TerminalBlock_Xinya_XY308-2.54-3P_1x03_P2.54mm_Horizontal; not fitted
Q3: Q_NMOS_GDS; SOT-23; Mrf_part AO3400-HXY; JLC C4748804
R21: 4.7k; R_0805_2012Metric
R39: 470R; R_0805_2012Metric
R40: 47k; R_0805_2012Metric

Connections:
/central_control_unit/1-Wire: J17.2, J18.2, J19.2, R21.2; also elsewhere on the board
/central_control_unit/temp_sensor_enable: R39.1; also elsewhere on the board
/central_control_unit/temp_sensors/temp_sens_gnd: J17.3, J18.3, J19.3, Q3.2 (D)
GND_LP: C13.2, Q3.3 (S), R40.2; also elsewhere on the board
unnamed: Q3.1 (G), R39.2, R40.1

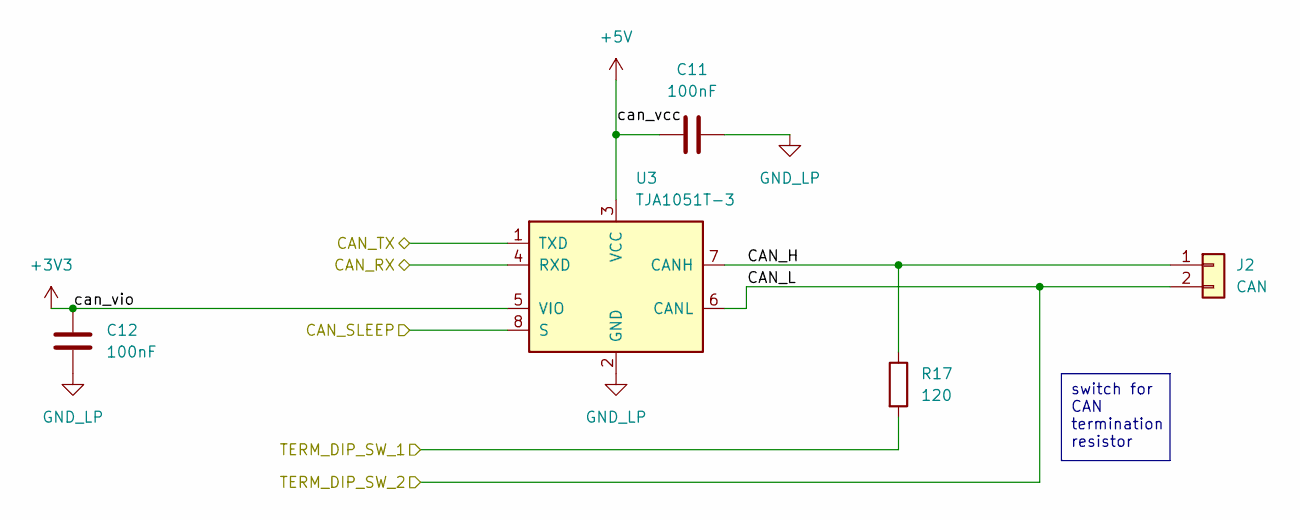
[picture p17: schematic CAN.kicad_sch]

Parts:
C11, C12: 100nF; C_0805_2012Metric
J2: CAN; TerminalBlock_Xinya_XY308-2.54-2P_1x02_P2.54mm_Horizontal
R17: 120; R_0805_2012Metric
U3: TJA1051T-3; SOIC-8_3.9x4.9mm_P1.27mm

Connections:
+5V: C11.1, U3.3 (VCC); also elsewhere on the board
/central_control_unit/CAN/CAN_H: J2.1, R17.1, U3.7 (CANH)
/central_control_unit/CAN/can_vio: C12.1, U3.5 (VIO)
/central_control_unit/can_rx: U3.4 (RXD); also elsewhere on the board
/central_control_unit/can_sleep: U3.8 (S); also elsewhere on the board
/central_control_unit/can_term_r_dip_1: R17.2; also elsewhere on the board
/central_control_unit/can_term_r_dip_2: J2.2, U3.6 (CANL); also elsewhere on the board
/central_control_unit/can_tx: U3.1 (TXD); also elsewhere on the board
GND_LP: C11.2, C12.2, U3.2 (GND); also elsewhere on the board

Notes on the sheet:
switch for CAN termination resistor

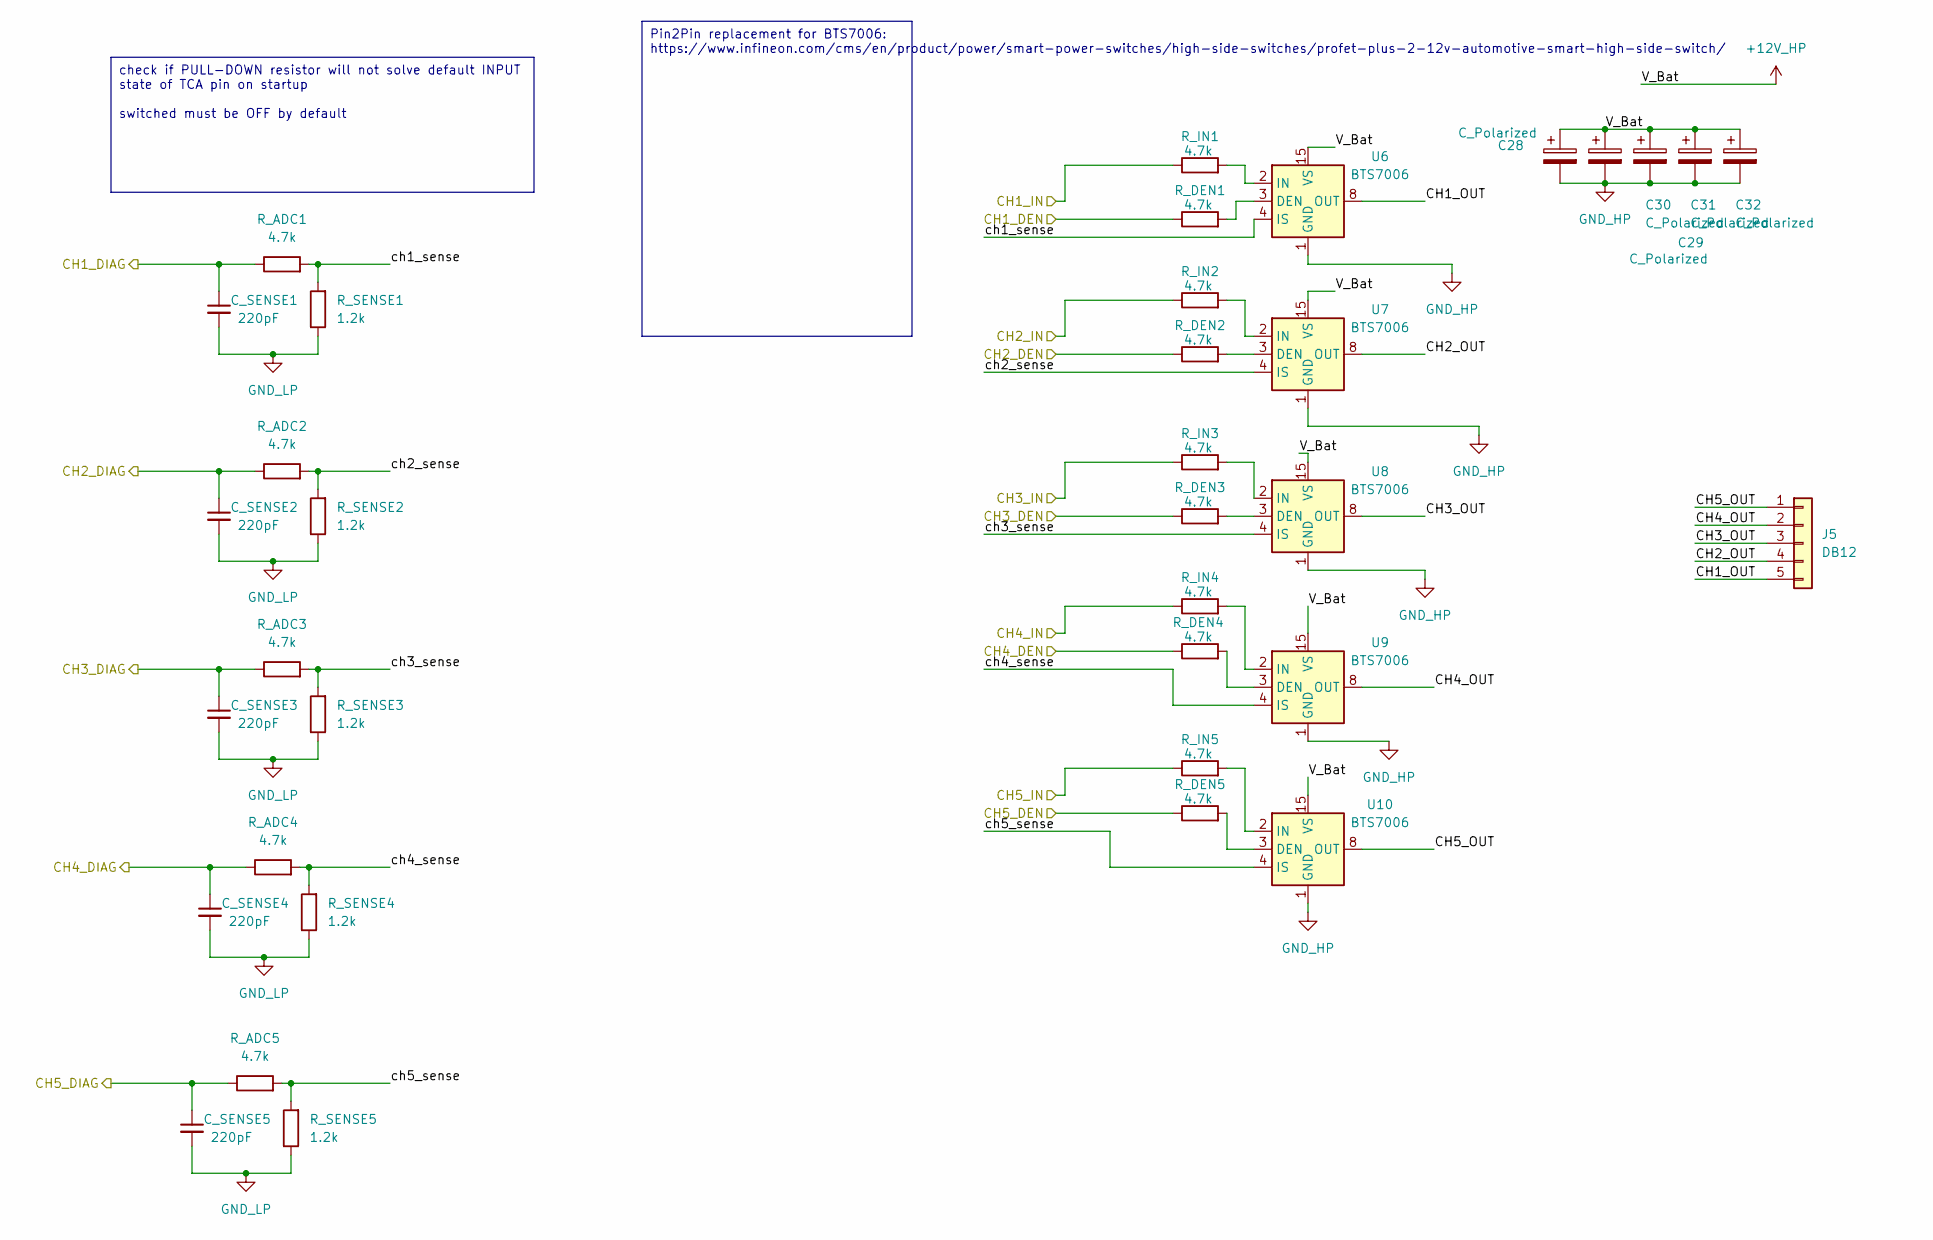
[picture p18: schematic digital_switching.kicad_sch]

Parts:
C28, C29, C30, C31, C32: C_Polarized; CP_Radial_D5.0mm_P2.50mm
C_SENSE1, C_SENSE2, C_SENSE3, C_SENSE4: 220pF; C_0805_2012Metric
C_SENSE5: 220pF; C_1210_3225Metric_Pad1.33x2.70mm_HandSolder
J5: DB12; 5p_terminal_DB12; LCSCc C2927513
R_ADC1, R_ADC2, R_ADC3, R_ADC4, R_ADC5: 4.7k; R_0805_2012Metric
R_DEN1, R_DEN2, R_DEN3, R_DEN4, R_DEN5: 4.7k; R_0805_2012Metric
R_IN1, R_IN2, R_IN3, R_IN4, R_IN5: 4.7k; R_0805_2012Metric
R_SENSE1, R_SENSE2, R_SENSE3, R_SENSE4, R_SENSE5: 1.2k; R_0805_2012Metric
U6: BTS7006; Infineon_PG-TSDSO-14-22; Mfr Part BTS7006-1EPP; Mouser 726-BTS70061EPPXUMA1
U7, U8, U9, U10: BTS7006; Infineon_PG-TSDSO-14-22

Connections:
+12V_HP: C28.1, C29.1, C30.1, C31.1, C32.1, U6.15 (VS), U7.15 (VS), U8.15 (VS), U9.15 (VS), U10.15 (VS); also elsewhere on the board
/central_control_unit/ch1_den: R_DEN1.1; also elsewhere on the board
/central_control_unit/ch1_diag: C_SENSE1.1, R_ADC1.1; also elsewhere on the board
/central_control_unit/ch1_in: R_IN1.1; also elsewhere on the board
/central_control_unit/ch2_den: R_DEN2.1; also elsewhere on the board
/central_control_unit/ch2_diag: C_SENSE2.1, R_ADC2.1; also elsewhere on the board
/central_control_unit/ch2_in: R_IN2.1; also elsewhere on the board
/central_control_unit/ch3_den: R_DEN3.1; also elsewhere on the board
/central_control_unit/ch3_diag: C_SENSE3.1, R_ADC3.1; also elsewhere on the board
/central_control_unit/ch3_in: R_IN3.1; also elsewhere on the board
/central_control_unit/ch4_den: R_DEN4.1; also elsewhere on the board
/central_control_unit/ch4_diag: C_SENSE4.1, R_ADC4.1; also elsewhere on the board
/central_control_unit/ch4_in: R_IN4.1; also elsewhere on the board
/central_control_unit/ch5_den: R_DEN5.1; also elsewhere on the board
/central_control_unit/ch5_diag: C_SENSE5.1, R_ADC5.1; also elsewhere on the board
/central_control_unit/digital_switching/CH1_OUT: J5.5, U6.8 (OUT), U6.9 (OUT), U6.10 (OUT), U6.12 (OUT), U6.13 (OUT), U6.14 (OUT)
/central_control_unit/digital_switching/CH2_OUT: J5.4, U7.8 (OUT), U7.9 (OUT), U7.10 (OUT), U7.12 (OUT), U7.13 (OUT), U7.14 (OUT)
/central_control_unit/digital_switching/CH3_OUT: J5.3, U8.8 (OUT), U8.9 (OUT), U8.10 (OUT), U8.12 (OUT), U8.13 (OUT), U8.14 (OUT)
/central_control_unit/digital_switching/CH4_OUT: J5.2, U9.8 (OUT), U9.9 (OUT), U9.10 (OUT), U9.12 (OUT), U9.13 (OUT), U9.14 (OUT)
/central_control_unit/digital_switching/CH5_IN: R_IN5.1; also elsewhere on the board
/central_control_unit/digital_switching/CH5_OUT: J5.1, U10.8 (OUT), U10.9 (OUT), U10.10 (OUT), U10.12 (OUT), U10.13 (OUT), U10.14 (OUT)
/central_control_unit/digital_switching/ch1_sense: R_ADC1.2, R_SENSE1.2, U6.4 (IS)
/central_control_unit/digital_switching/ch2_sense: R_ADC2.2, R_SENSE2.2, U7.4 (IS)
/central_control_unit/digital_switching/ch3_sense: R_ADC3.2, R_SENSE3.2, U8.4 (IS)
/central_control_unit/digital_switching/ch4_sense: R_ADC4.2, R_SENSE4.2, U9.4 (IS)
/central_control_unit/digital_switching/ch5_sense: R_ADC5.2, R_SENSE5.2, U10.4 (IS)
GND_HP: C28.2, C29.2, C30.2, C31.2, C32.2, U6.1 (GND), U7.1 (GND), U8.1 (GND), U9.1 (GND), U10.1 (GND); also elsewhere on the board
GND_LP: C_SENSE1.2, C_SENSE2.2, C_SENSE3.2, C_SENSE4.2, C_SENSE5.2, R_SENSE1.1, R_SENSE2.1, R_SENSE3.1, R_SENSE4.1, R_SENSE5.1; also elsewhere on the board
unnamed: R_DEN1.2, U6.3 (DEN)
unnamed: R_IN1.2, U6.2 (IN)
unnamed: R_DEN2.2, U7.3 (DEN)
unnamed: R_IN2.2, U7.2 (IN)
unnamed: R_DEN3.2, U8.3 (DEN)
unnamed: R_IN3.2, U8.2 (IN)
unnamed: R_DEN4.2, U9.3 (DEN)
unnamed: R_IN4.2, U9.2 (IN)
unnamed: R_DEN5.2, U10.3 (DEN)
unnamed: R_IN5.2, U10.2 (IN)

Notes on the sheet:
check if PULL-DOWN resistor will not solve default INPUT state of TCA pin on startup switched must be OFF by default
Pin2Pin replacement for BTS7006: https://www.infineon.com/cms/en/product/power/smart-power-switches/high-side-switches/profet-plus-2-12v-automotive-smart-high-side-switch/

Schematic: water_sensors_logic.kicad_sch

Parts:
J10: water_sensor_conn; TerminalBlock_Xinya_XY308-2.54-5P_1x05_P2.54mm_Horizontal
J13: Conn_01x02; TerminalBlock_Xinya_XY308-2.54-2P_1x02_P2.54mm_Horizontal
R16, R26: 100k; R_0805_2012Metric
R28, R29, R30, R31: 1M; R_0805_2012Metric
U5, U14: LM339_4ch; SOIC-14_3.9x8.7mm_P1.27mm; Mfr Part LM339DR; lcsc C7948

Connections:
/central_control_unit/GREY_FULL: U5.2 (OUT1); also elsewhere on the board
/central_control_unit/WS_LVL_25: U14.13 (OUT4); also elsewhere on the board
/central_control_unit/WS_LVL_50: U14.14 (OUT3); also elsewhere on the board
/central_control_unit/WS_LVL_75: U14.1 (OUT2); also elsewhere on the board
/central_control_unit/WS_LVL_100: U14.2 (OUT1); also elsewhere on the board
/central_control_unit/water_sensors_logic/grey_water_probe: J13.2, U5.4 (IN1-)
/central_control_unit/water_sensors_logic/probe_1: J10.5, R28.2, U14.4 (IN1-)
/central_control_unit/water_sensors_logic/probe_2: J10.4, R29.2, U14.6 (IN2-)
/central_control_unit/water_sensors_logic/probe_3: J10.3, R30.2, U14.8 (IN3-)
/central_control_unit/water_sensors_logic/probe_4: J10.2, R31.2, U14.10 (IN4-)
/central_control_unit/water_sensors_logic/ws_vref: R16.1, R26.2, U5.5 (IN1+), U14.5 (IN1+), U14.7 (IN2+), U14.9 (IN3+), U14.11 (IN4+)
GND_LP: J10.1, J13.1, R26.1, U5.12 (GND), U14.12 (GND); also elsewhere on the board

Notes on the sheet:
output is HIGH when probe NOT IN water output is LOW when probe IN water

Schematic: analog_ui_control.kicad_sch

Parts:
C16, C26: C_Polarized; CP_Radial_D5.0mm_P2.50mm
C25: 10uF; C_0805_2012Metric
C27: 100nF; C_0805_2012Metric
J3: Conn_01x08; TerminalBlock_Xinya_XY308-2.54-8P_1x08_P2.54mm_Horizontal

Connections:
+5V: C16.1, C25.2, C26.1, C27.2, J3.1; also elsewhere on the board
/central_control_unit/analog_ui_rmt_led: J3.3; also elsewhere on the board
/central_control_unit/btn_1: J3.4; also elsewhere on the board
/central_control_unit/btn_2: J3.5; also elsewhere on the board
/central_control_unit/btn_3: J3.6; also elsewhere on the board
/central_control_unit/btn_4: J3.7; also elsewhere on the board
/central_control_unit/btn_5: J3.8; also elsewhere on the board
GND_LP: C16.2, C25.1, C26.2, C27.1, J3.2; also elsewhere on the board

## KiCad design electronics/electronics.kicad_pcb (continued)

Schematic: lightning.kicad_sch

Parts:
C1, C3: C_Polarized; CP_Radial_D5.0mm_P2.50mm; not fitted
C2, C4: C; C_0805_2012Metric; not fitted
F6: 5A; ATO_fuse_holder; LCSC_part C2935871
J1: leds_ch1; TerminalBlock_Xinya_XY308-2.54-3P_1x03_P2.54mm_Horizontal
J20: leds_ch2; TerminalBlock_Xinya_XY308-2.54-3P_1x03_P2.54mm_Horizontal
J26: leds_ch3; TerminalBlock_Xinya_XY308-2.54-3P_1x03_P2.54mm_Horizontal
J27: leds_ch4; TerminalBlock_Xinya_XY308-2.54-3P_1x03_P2.54mm_Horizontal
Q6: Q_NMOS_GDS; SOT-23; Mrf_part AO3400-HXY; JLC C4748804
R1: 47k; R_0805_2012Metric
R2: 470R; R_0805_2012Metric
U2: ISO6740; SOIC-16W_7.5x10.3mm_P1.27mm; not fitted
U4: generic_dcdc; not fitted

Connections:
+5V_LEDs: C3.1, C4.1, J1.3, J20.3, J26.3, J27.3, U4.3 (VOUT)
+12V_HP: F6.1; also elsewhere on the board
/central_control_unit/LED_CH1: J1.2, U2.3 (INA), U2.14 (OUTA); also elsewhere on the board
/central_control_unit/LED_CH2: J20.2, U2.4 (INB), U2.13 (OUTB); also elsewhere on the board
/central_control_unit/LED_CH3: J26.2, U2.5 (INC), U2.12 (OUTC); also elsewhere on the board
/central_control_unit/LED_CH4: J27.2, U2.6 (IND), U2.11 (OUTD); also elsewhere on the board
/central_control_unit/led_en: R2.1; also elsewhere on the board
GND_HP: C1.2, C2.2, Q6.3 (S), R1.2, U2.9 (GND2), U2.15 (GND2); also elsewhere on the board
GND_LEDs: C3.2, C4.2, J1.1, J20.1, J26.1, J27.1, U4.4 (GND)
unnamed: Q6.2 (D), U4.2 (GND)
unnamed: Q6.1 (G), R1.1, R2.2
unnamed: U2.2 (GND1), U2.8 (GND1)
unnamed: C1.1, C2.1, F6.2, U4.1 (VIN)

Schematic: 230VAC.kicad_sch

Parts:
C9: 4.7uF; C_0805_2012Metric
C34: C; C_Disc_D3.0mm_W2.0mm_P2.50mm
D2: 1N4148W; D_SOD-123; MFG part nr 1N4148W; lcsc C917030
J21, J22: Conn_01x02; TerminalBlock_Xinya_XY308-2.54-2P_1x02_P2.54mm_Horizontal
Q5: Q_NMOS_GDS; SOT-23; Mrf_part AO3400-HXY; JLC C4748804
R22: 470R; R_0805_2012Metric
R23, R24: 100k; R_Axial_DIN0207_L6.3mm_D2.5mm_P7.62mm_Horizontal
R25: 4.7kΩ; R_0805_2012Metric
R41: 47k; R_0805_2012Metric
RL1: AZSR131-1AE-12D; PRE29-same-sky; MFG Part Nr PRE29-5V-S-450; not fitted
U17: LTV-814; DIP-4_W7.62mm; mouser 859-LTV-814S-TA1-A

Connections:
+3.3V: R25.1; also elsewhere on the board
+5V: D2.1 (K), RL1.2; also elsewhere on the board
/central_control_unit/230VAC/N_230VAC: J21.2, R24.1
/central_control_unit/230VAC/P_230VAC: J21.1, R23.1
/central_control_unit/ac_detect: C9.1, R25.2, U17.4; also elsewhere on the board
/central_control_unit/relay_out: R22.1; also elsewhere on the board
GND_LP: C9.2, Q5.3 (S), R41.2, U17.3; also elsewhere on the board
unnamed: C34.1, R23.2, U17.1
unnamed: C34.2, R24.2, U17.2
unnamed: D2.2 (A), Q5.2 (D), RL1.1
unnamed: J22.1, RL1.4
unnamed: J22.2, RL1.3
unnamed: Q5.1 (G), R22.2, R41.1

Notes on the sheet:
230VAC Detection
25mA LED current

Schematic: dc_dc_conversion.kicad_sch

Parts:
D1, D13, D14: LED; LED_1206_3216Metric
D15: D_Schottky; D_SMA
FB1: FerriteBead 47 Ohm; L_Walsin_WLFM201609x
J25: header; PinHeader_1x02_P2.54mm_Vertical
Q1: Q_NMOS_DGS; SOT-323_SC-70
Q2: Q_PMOS_DGS; SOT-323_SC-70
R3, R4, R18, R33, R34, R35: 4k7; R_0805_2012Metric
R36: 470R; R_0805_2012Metric
R37, R38: 47k; R_0805_2012Metric
U1: TLV1117-33; SOT-223-3_TabPin2; JLC C37359
U18: mini360; not fitted

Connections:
+3.3V: R4.2, U1.2 (VO); also elsewhere on the board
+5V: J25.2, R18.2, U1.3 (VI), U18.3 (VOUT); also elsewhere on the board
+12V: Q2.3 (S), R33.2, R38.1, U18.1 (VIN); also elsewhere on the board
/central_control_unit/USB_VIN: D15.2 (A), R36.2; also elsewhere on the board
/central_control_unit/dc_dc_conversion/USB_VBUS: D15.1 (K), J25.1
/central_control_unit/dc_dc_conversion/vin: Q2.1 (D)
GND_HP: FB1.2, U18.2 (GND), U18.4 (GND); also elsewhere on the board
GND_LP: D1.1 (K), D13.1 (K), D14.1 (K), FB1.1, Q1.3 (S), R37.2, U1.1 (GND); also elsewhere on the board
unnamed: D1.2 (A), R35.1
unnamed: D13.2 (A), R4.1
unnamed: D14.2 (A), R3.1
unnamed: Q1.1 (D), Q2.2 (G), R38.2
unnamed: Q1.2 (G), R36.1, R37.1
unnamed: R3.2, R18.1
unnamed: R33.1, R34.1
unnamed: R34.2, R35.2

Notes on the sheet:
USB_VSYS disconnets 12V to 5V DC/DC converter
Green LEDs
5V 6A max

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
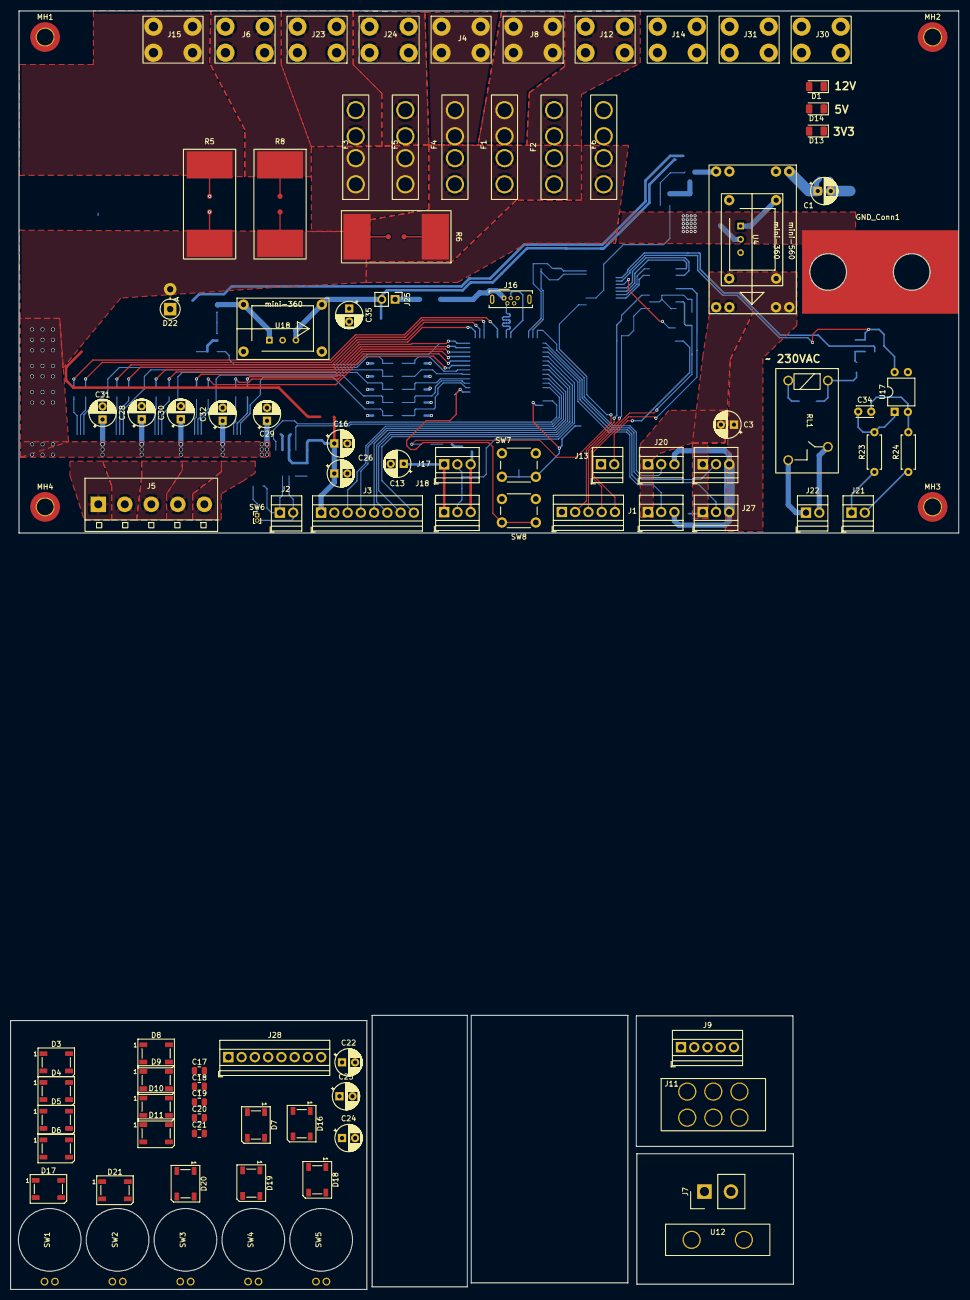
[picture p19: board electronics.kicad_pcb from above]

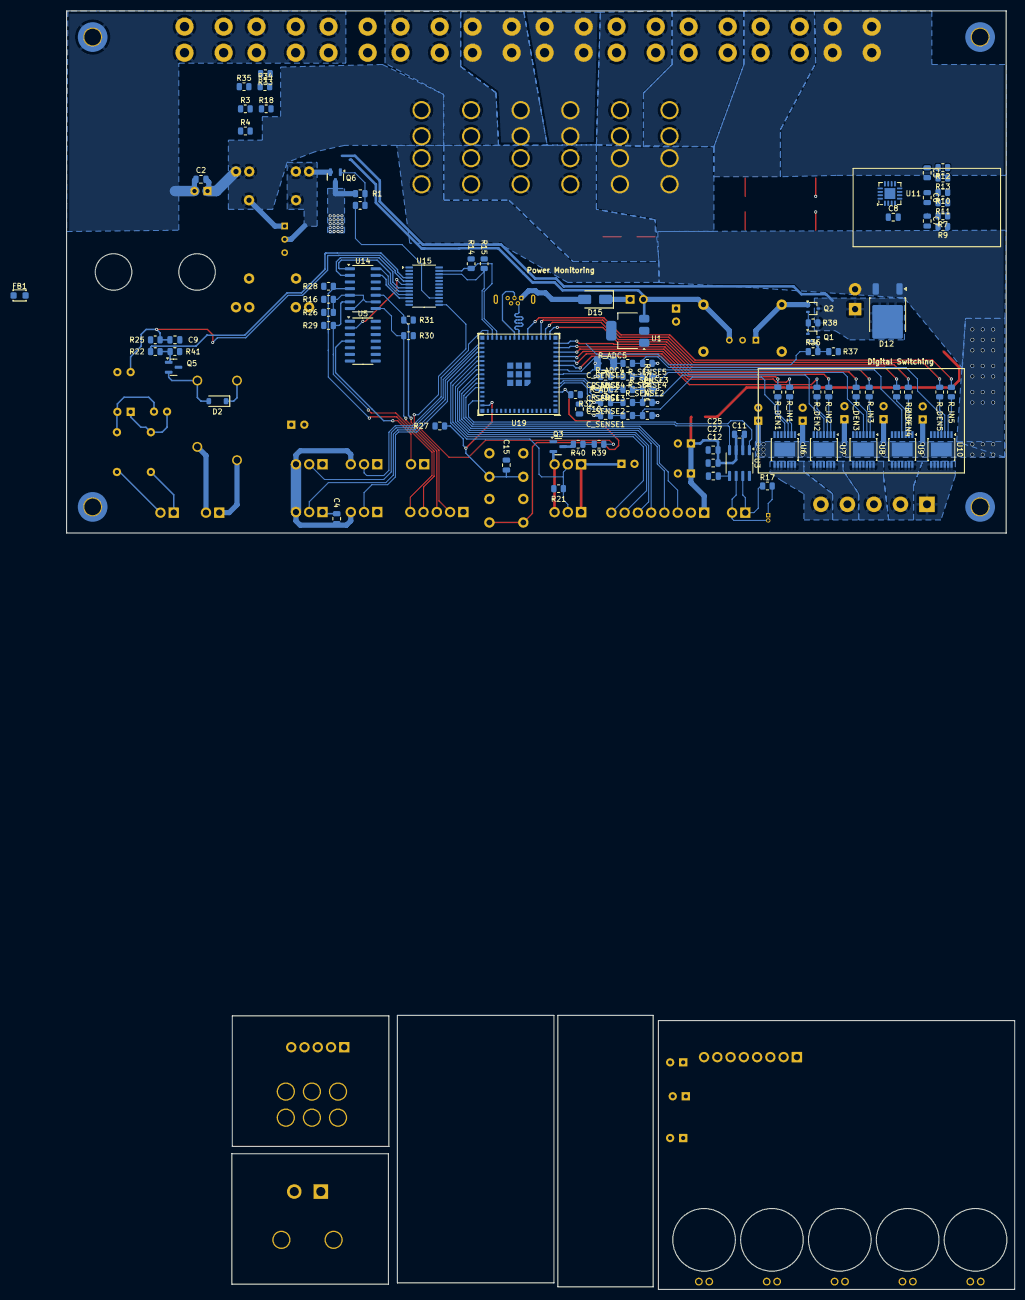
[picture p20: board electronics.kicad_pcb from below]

Board: 2 copper layers, 180.0 x 100.0 mm, 190 parts (93 on the bottom side), 154 nets.

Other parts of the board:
C35: C_Polarized; CP_Radial_D5.0mm_P2.50mm

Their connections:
+5V: C35.1; also elsewhere on the board
GND_HP: C35.2; also elsewhere on the board

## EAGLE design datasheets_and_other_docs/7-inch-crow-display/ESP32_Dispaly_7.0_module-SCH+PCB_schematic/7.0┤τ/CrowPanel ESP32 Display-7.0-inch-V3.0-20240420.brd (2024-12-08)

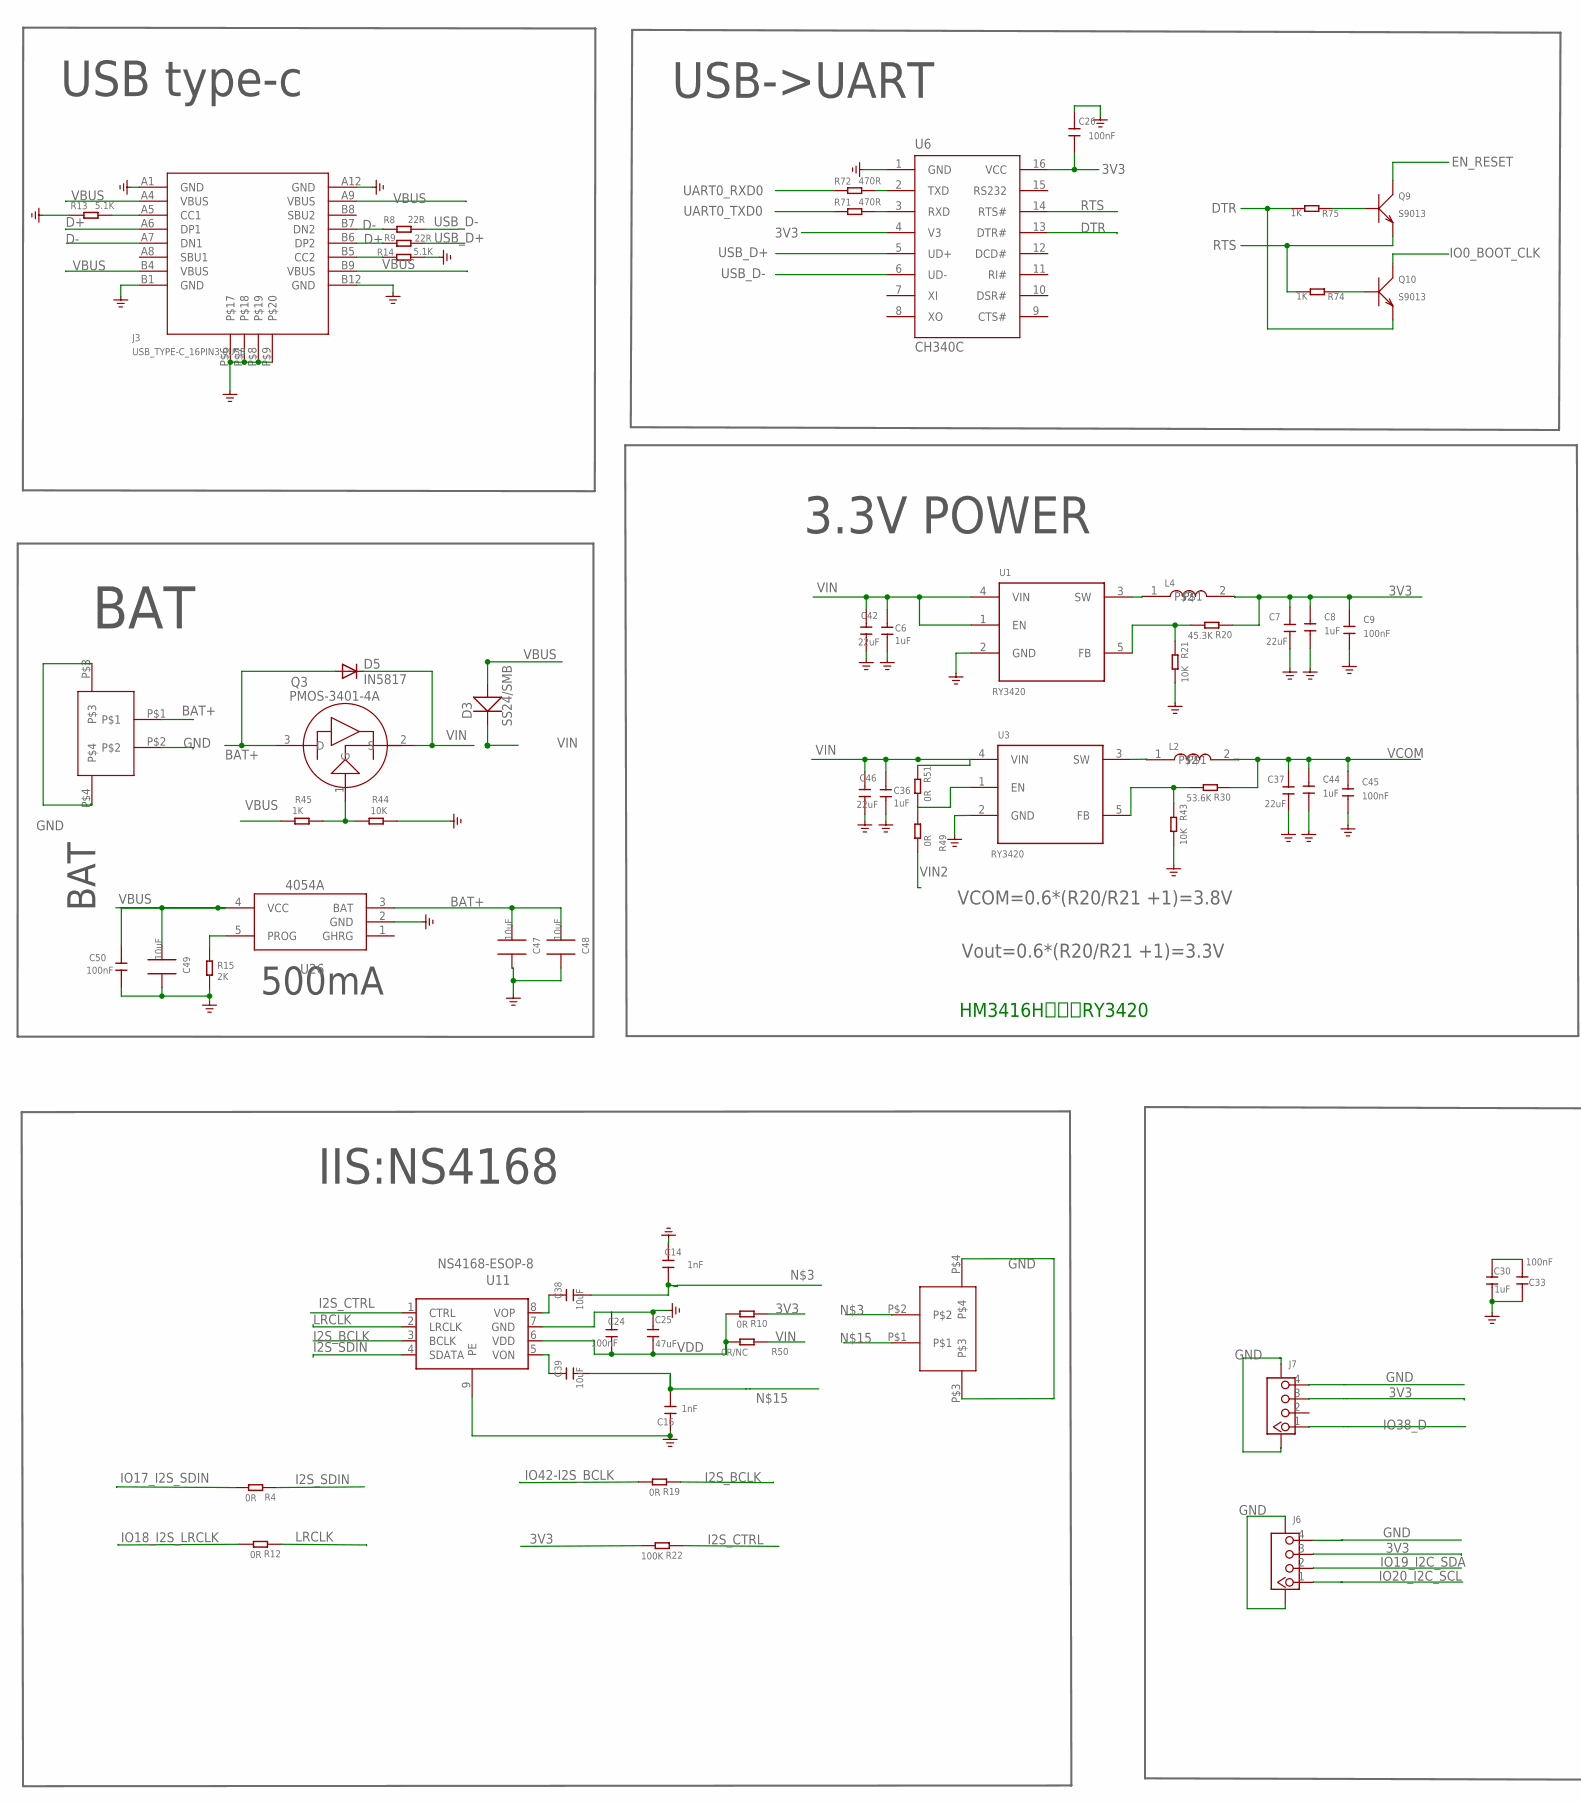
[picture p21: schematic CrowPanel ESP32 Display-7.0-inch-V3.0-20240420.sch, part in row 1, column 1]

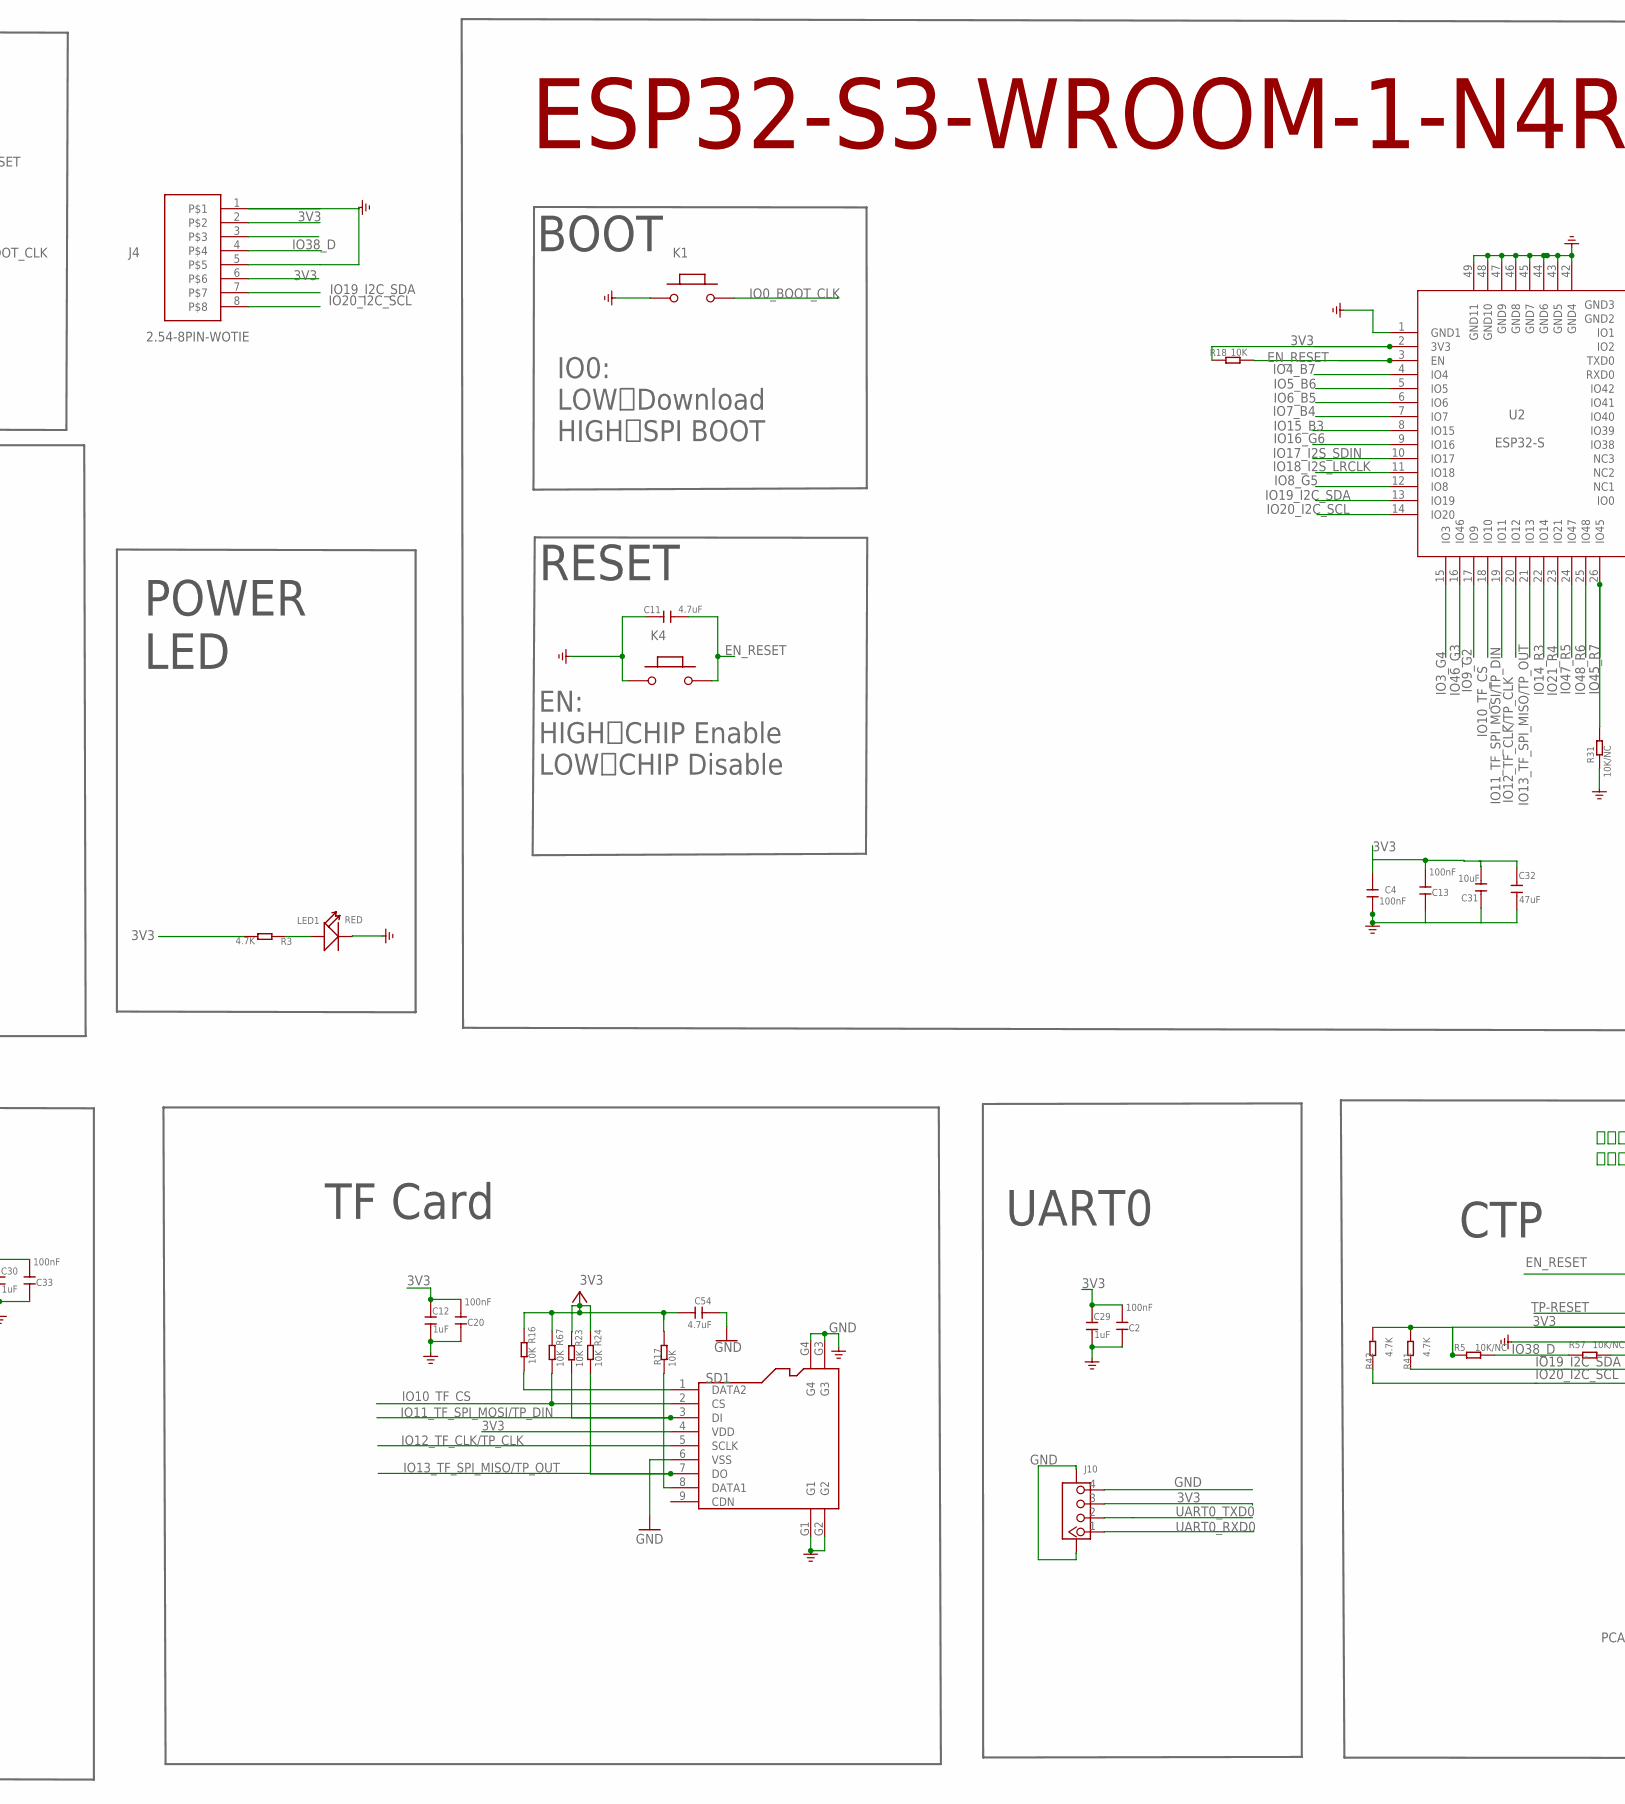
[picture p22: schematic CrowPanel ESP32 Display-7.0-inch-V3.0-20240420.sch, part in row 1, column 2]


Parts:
C1: 0.1uF/NC; DISCRETE_C0603
C2, C4, C13, C20, C22, C24, C33, C50: 100nF; C0603
C3, C6, C8, C15, C18, C36, C44: 1uF; 0603
C5: 1uF; C0603
C7, C10, C19, C23, C37, C42, C43, C46: 22uF; 0805
C9, C17, C21, C26, C34, C35, C45, C76: 100nF; 0603
C11: 4.7uF; 0603
C12, C29, C30: 1uF; DISCRETE_C0603
C14, C16: 1nF; C0603
C25, C32: 47uF; 0805
C27, C28: 100NF; 0603
C31: 10uF; DISCRETE_C0603
C38, C39: 10uF; C0603
C40, C41: 1uF; 0805
C47, C48, C49: 10uF; 0805_S
C51: 4.7uF/NC; 0603
C52: 100NF; A_XBJ_0603
C54: 4.7uF; DISCRETE_C0603
D1, D6: SS24B/SMB; 214AB
D2: BZT52C-18V; DISCRETE_SOD123
D3: SS24/SMB; 214AB
D4: BZT52C-8.2V; DISCRETE_SOD123
D5: IN5817; DO-214AC
IC1: PCA9557-16P; TSSOP16
J1, J5: PH2.0WT-2PIN
J2: 7.0-DIANRONG-50PIN-0.5MM; 7.0-DAINRONG-50PIN-0.5MM
J3: USB_TYPE-C_16PIN3.0USB; KEVIN_3.0TYPEC-SMD
J4: 2.54-8PIN-WOTIE; 2.54-8P-WOTIE
J6, J7, J10: CONNECTOR_TWIG-4P-2.0-SMD-FEMALE-REINFORCE90D; CONNECTOR_4P-SMD-2.0-90D
K1, K4: BUTTON; 157SW
L1, L2, L4: L-0530; CD54_CD54
L5: CD32_6.8uH; CD32
LED1: RED; DISCRETE_LED-0603
P2, P4: FPC-6PIN-0.5MM
Q1, Q2: BAT54S; SOT23-3
Q3, Q4, Q30: PMOS-3401-4A; SOT-23
Q5, Q6: S8050; SPARKFUN_SOT23
Q9, Q10: S9013; SOT23@1
R1: 75K; DISCRETE_R0603
R2: 10.5K; DISCRETE_R0603
R3, R41, R42, R61: 4.7K; DISCRETE_R0603
R4, R10, R12, R19, R25, R46, R49, R51, R53: 0R; DISCRETE_R0603
R5, R32, R35, R37, R39, R57: 10K/NC; DISCRETE_R0603
R6: 15K; DISCRETE_R0603
R7, R13, R14: 5.1K; DISCRETE_R0603
R8, R9: 22R; DISCRETE_R0603
R11: 100R; R0603
R15: 2K; DISCRETE_R0603
R16, R17, R18, R21, R23, R24, R33, R34, R36, R43, R44, R67, R90: 10K; DISCRETE_R0603
R20: 45.3K; DISCRETE_R0603
R22: 100K; DISCRETE_R0603
R26, R38: 0R; R0603
R27, R28: 47K; DISCRETE_R0603
R29: 1.8R 1%; DISCRETE_R0603
R30: 53.6K; DISCRETE_R0603
R31: 10K/NC; R0603
R40: 0R/NC; R0603
R45, R74, R75: 1K; DISCRETE_R0603
R47: NC/1K; DISCRETE_R0603
R48, R54, R172: 100K; R0603
R50, R52, R56, R59, R60: 0R/NC; DISCRETE_R0603
R55: 100k; R0603
R58: 10k; R0603
R71, R72: 470R; DISCRETE_R0603
R91: 7.5K; DISCRETE_R0603
SD1: HOLDER-MICROSD-9P; 9P-SMD-W/-RING
U1, U3: RY3420; A_XBJ_SOT23-5
U2: ESP32-S; ESP32-S3
U4: MT9201; SOT23-6
U5: LP3318; LP3318_SOT23-5
U6: CH340C; SOP-16
U11: NS4168-ESOP-8
U26: 4054A; SOP23-5

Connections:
3V3: C2.1, C4.2, C7.2, C8.2, C9.2, C12.2, C13.1, C20.1, C26.1, C29.2, C30.2, C31.2, C32.2, C33.1, C52.1, C54.2, IC1.16 (VCC), J4.2, J4.6, J6.3, J7.3, J10.3, L4.2, P2.5 (2), P4.5 (2), Q4.2 (S), R3.2, R5.1, R10.1, R16.1, R17.1, R18.1, R20.1, R22.2, R23.1, R24.1, R41.2, R42.2, R47.2, R48.1, R56.1, R61.2, R67.1, SD1.4 (VDD), U2.2 (3V3), U6.4 (V3), U6.16 (VCC)
AVDD_10V: C10.2, C15.2, C17.2, D1.2 (-), J2.P$8 (AVDD), Q1.1, R1.1, R90.1
BAT+: C47.2, C48.2, D5.A, J1.P$1, Q3.3 (D), U26.3 (BAT)
D+: J3.A6 (DP1), J3.B6 (DP2), R9.1
D-: J3.A7 (DN1), J3.B7 (DN2), R8.1
DCLK1: C1.2, J2.P$14 (DCLK), R38.2
DTR: Q10.2 (E), R75.2, U6.13 (DTR#)
EN_RESET: C11.1, K4.2, Q9.3 (C), R18.2, R40.1, R46.2, R54.2, U2.3 (EN)
GND: C1.1, C2.2, C3.1, C4.1, C5.2, C6.1, C7.1, C8.1, C9.1, C10.1, C11.2, C12.1, C13.2, C14.2, C15.1, C16.2, C17.1, C18.1, C19.1, C20.2, C21.1, C22.1, C23.1, C24.2, C25.2, C26.2, C29.1, C30.1, C31.1, C32.1, C33.2, C34.1, C35.1, C36.1, C37.1, C40.1, C41.1, C42.1, C43.1, C44.1, C45.1, C46.1, C47.1, C48.1, C49.1, C50.2, C51.2, C52.2, C54.1, C76.1, D2.+, D4.-, IC1.3 (A0), IC1.4 (A1), IC1.5 (A2), IC1.8 (VSS), J1.P$2, J1.P$3, J1.P$4, J2.P$3 (GND3), J2.P$13 (GND2), J2.P$15 (GND1), J2.P$16 (R0), J2.P$17 (R1), J2.P$18 (R2), J2.P$24 (G0), J2.P$25 (G1), J2.P$32 (B0), J2.P$33 (B1), J2.P$34 (B2), J2.P$46 (GND), J3.A1 (GND), J3.A12 (GND), J3.B1 (GND), J3.B12 (GND), J3.P$6, J3.P$7, J3.P$8, J3.P$9, J4.1, J4.5, J5.P$3, J5.P$4, J6.4, J6.SS1, J6.SS2, J7.4, J7.SS1, J7.SS2, J10.4, J10.SS1, J10.SS2, K1.1, K4.1, LED1.-, P2.4 (3), P2.7, P2.8, P4.4 (3), P4.7, P4.8, Q2.2, Q5.2 (E), Q6.2 (E), R2.2, R13.1, R14.2, R15.2, R21.2, R27.2, R28.2, R29.2, R31.1, R33.1, R35.1, R37.1, R43.2, R44.1, R55.1, R58.1, R91.2, SD1.6 (VSS), SD1.G1, SD1.G2, SD1.G3, SD1.G4, U1.2 (GND), U2.1 (GND1), U2.40 (GND2), U2.41 (GND3), U2.42 (GND4), U2.43 (GND5), U2.44 (GND6), U2.45 (GND7), U2.46 (GND8), U2.47 (GND9), U2.48 (GND10), U2.49 (GND11), U3.2 (GND), U4.2 (2-GND), U5.2 (GND), U6.1 (GND), U11.7 (GND), U11.9 (PE), U26.2 (GND)
I2S_BCLK: R19.1, U11.3 (BCLK)
I2S_CTRL: R22.1, U11.1 (CTRL)
I2S_SDIN: R4.1, U11.4 (SDATA)
INTE: IC1.7 (IO1), P2.3 (4), P4.3 (4), R57.2
IO0_BOOT_CLK: K1.2, Q10.3 (C), R38.1, U2.27 (IO0)
IO1_G7: J2.P$31 (G7), U2.39 (IO1)
IO2_LCD_BL_CTR: R11.2, U2.38 (IO2), U4.4 (4-EN)
IO3_G4: J2.P$28 (G4), U2.15 (IO3)
IO4_B7: J2.P$39 (B7), U2.4 (IO4)
IO5_B6: J2.P$38 (B6), U2.5 (IO5)
IO6_B5: J2.P$37 (B5), U2.6 (IO6)
IO7_B4: J2.P$36 (B4), U2.7 (IO7)
IO8_G5: J2.P$29 (G5), U2.12 (IO8)
IO9_G2: J2.P$26 (G2), U2.17 (IO9)
IO10_TF_CS: R67.2, SD1.2 (CS), U2.18 (IO10)
IO11_TF_SPI_MOSI/TP_DIN: R23.2, SD1.3 (DI), U2.19 (IO11)
IO12_TF_CLK/TP_CLK: SD1.5 (SCLK), U2.20 (IO12)
IO13_TF_SPI_MISO/TP_OUT: R24.2, SD1.7 (DO), U2.21 (IO13)
IO14_R3: J2.P$19 (R3), U2.22 (IO14)
IO15_B3: J2.P$35 (B3), U2.8 (IO15)
IO16_G6: J2.P$30 (G6), U2.9 (IO16)
IO17_I2S_SDIN: R4.2, U2.10 (IO17)
IO18_I2S_LRCLK: R12.2, U2.11 (IO18)
IO19_I2C_SDA: IC1.2 (SDA), J4.7, J6.2, P2.2 (5), P4.2 (5), R41.1, U2.13 (IO19)
IO20_I2C_SCL: IC1.1 (SCL), J4.8, J6.1, P2.1 (6), P4.1 (6), R42.1, U2.14 (IO20)
IO21_R4: J2.P$20 (R4), U2.23 (IO21)
IO38_D: J4.4, J7.1, R5.2, R57.1, U2.31 (IO38)
IO39_HSYNC: J2.P$40 (HSYNC), U2.32 (IO39)
IO40_VSYNC: J2.P$41 (VSYNC), U2.33 (IO40)
IO41_DE: J2.P$42 (DE), U2.34 (IO41)
IO42-I2S_BCLK: R19.2, U2.35 (IO42)
IO45_R7: J2.P$23 (R7), R31.2, U2.26 (IO45)
IO46_G3: J2.P$27 (G3), U2.16 (IO46)
IO47_R5: J2.P$21 (R5), U2.24 (IO47)
IO48_R6: J2.P$22 (R6), U2.25 (IO48)
L/R: J2.P$12 (L/R), R34.1, R35.2
LCD-POWER-C: IC1.10 (IO3), R60.2
LCD-RESET: IC1.9 (IO2), R59.2
LCD_LEDA: C19.2, C21.2, D6.2 (-), J2.P$49 (LED-A), J2.P$50 (LED_A), U4.5 (5-OV)
LCD_LEDK: J2.P$47 (LED-K), J2.P$48 (LED_K), R29.1, U4.3 (3-FB)
LRCLK: R12.1, U11.2 (LRCLK)
unnamed: LED1.+, R3.1
unnamed: J2.P$45 (VCOM), R25.2
unnamed: C14.1, C38.1, J5.P$2
unnamed: J2.P$5 (VCOM1), R26.2
unnamed: C38.2, U11.8 (VOP)
unnamed: R1.2, R2.1, U5.3 (FB)
unnamed: C39.2, U11.5 (VON)
unnamed: C27.2, C28.2, D1.1 (+), L1.2, U5.1 (LX)
unnamed: C27.1, Q1.3
unnamed: J3.A5 (CC1), R13.2
unnamed: J2.P$43 (MODE), R36.1, R37.2
unnamed: L4.1, U1.3 (SW)
unnamed: J2.P$4 (DITHB), R39.1
unnamed: C16.1, C39.1, J5.P$1
unnamed: D6.1 (+), L5.2, U4.1 (1-SW)
unnamed: J3.B5 (CC2), R14.1
unnamed: R30.2, R43.1, U3.5 (FB)
unnamed: L2.1, U3.3 (SW)
unnamed: R20.2, R21.1, U1.5 (FB)
unnamed: Q3.1 (G), R44.2, R45.1
unnamed: R15.1, U26.5 (PROG)
unnamed: Q5.1 (B), R11.1, R58.2
unnamed: C28.1, Q2.3
unnamed: R49.1, R51.2, U3.1 (EN)
unnamed: Q4.1 (G), Q6.3 (C), R48.2
unnamed: C35.2, Q1.2, R7.1
unnamed: C34.2, Q2.1, R6.1
unnamed: R52.2, R53.1, U5.4 (EN)
unnamed: Q9.1 (B), R75.1
unnamed: Q6.1 (B), R54.1, R55.2, R60.1
unnamed: Q5.3 (C), Q30.1 (G), R172.2
unnamed: Q10.1 (B), R74.1
unnamed: R72.2, U6.2 (TXD)
unnamed: R71.2, U6.3 (RXD)
unnamed: R16.2, SD1.1 (DATA2)
unnamed: R17.2, SD1.8 (DATA1)
unnamed: IC1.15 (RESET/), R61.1
RTS: Q9.2 (E), R74.2, U6.14 (RTS#)
TFT-3V3: C5.1, C22.2, J2.P$44 (DVDD), Q4.3 (D), R32.2, R34.2, R36.2, R39.2, R56.2
TFT_RESET: C51.1, J2.P$7 (RESET), R46.1, R47.1, R59.1
TP-RESET: IC1.6 (IO0), P2.6 (1), P4.6 (1), R40.2
U/D: J2.P$11 (U/D), R32.1, R33.2
UART0_RXD0: J10.1, R72.1, U2.36 (RXD0)
UART0_TXD0: J10.2, R71.1, U2.37 (TXD0)
USB_D+: R9.2, U6.5 (UD+)
USB_D-: R8.2, U6.6 (UD-)
VBUS: C49.2, C50.1, D3.1 (+), J3.A4 (VBUS), J3.A9 (VBUS), J3.B4 (VBUS), J3.B9 (VBUS), R45.2, U26.4 (VCC)
VCOM: C37.2, C44.2, C45.2, C76.2, L2.2, R25.1, R26.1, R30.1, R90.2, R91.1
VDD: C24.1, C25.1, R10.2, R50.2, U11.6 (VDD)
VGH+18V: C40.2, D2.-, J2.P$10 (VGH), R7.2, R27.1
VGL-8.2V: C41.2, D4.+, J2.P$9 (VGL), R6.2, R28.1
VIN: C3.2, C6.2, C23.2, C36.2, C42.2, C46.2, D3.2 (-), D5.C, L1.1, Q3.2 (S), Q30.2 (S), R50.1, R51.1, R52.1, R172.1, U1.1 (EN), U1.4 (VIN), U3.4 (VIN), U5.5 (VIN)
VIN2: C18.2, C43.2, L5.1, Q30.3 (D), R49.2, R53.2, U4.6 (6-VIN)

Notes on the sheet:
Vout=0.6*(R20/R21 +1)=3.3V
3.3V POWER
UART0
ESP32-S3-WROOM-1-N4R8
USB type-c
BAT
IO0: LOW：Download HIGH：SPI BOOT
EN: HIGH：CHIP Enable LOW：CHIP Disable
USB->UART
IIS:NS4168
TF Card
BOOT
RESET
POWER LED
LCD+TP
CTP
Iout=0.2/R29
L/R和U/D，预留上下拉
数据传输模式选择，预留上下拉
R37/R36选DE和H/V
Vout=0.6*(R20/R21 +1)=10V
正负压源
LCD恒流驱动
默认使用右边P4的触摸接口，如需更换使用左边P2触摸接口,BOM需要更改使用P2
默认使用右边P4的触摸接口，如需更换使用左边P2触摸接口,PCB的排线孔也要更改
HM3416H更换为RY3420
VCOM=0.6*(R20/R21 +1)=3.8V
500mA
PCA9557 ADDRESS:
0X18
PCA9557PW,118


Board: 2 copper layers, 181.1 x 103.9 mm, 169 parts (1 on the bottom side), 103 nets.

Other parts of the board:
U$10: 7.0底框
U$15: 7.0板框
U$76: LOGE-2.0
U$78: LOGLE

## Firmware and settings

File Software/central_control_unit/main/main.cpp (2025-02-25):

/* pthread/std::thread example

   This example code is in the Public Domain (or CC0 licensed, at your option.)

   Unless required by applicable law or agreed to in writing, this
   software is distributed on an "AS IS" BASIS, WITHOUT WARRANTIES OR
   CONDITIONS OF ANY KIND, either express or implied.
*/

#include <iostream>
#include <thread>
#include <chrono>
#include <memory>
#include <string>
#include <sstream>
#include <esp_pthread.h>
#include <freertos/FreeRTOS.h>
#include <freertos/task.h>
#include <esp_log.h>

#include <esp_io_expander.h>
#include "esp_io_expander_tca95xx_16bit.h"
#include "esp_log.h"
#include <gpio_cxx.hpp>
#include "i2c_cxx.hpp"
#include "cd74hc_mux.hpp"

#include "soc/soc_caps.h"
#include "esp_adc/adc_oneshot.h"
#include "esp_adc/adc_cali.h"
#include "esp_adc/adc_cali_scheme.h"
#include "esp_timer_cxx.hpp"
#include <bits/stdc++.h>
#include "esp_timer_cxx.hpp"

#include "analog_ui.h"
#include "temp_sensor.h"
#include "water_sensor.h"
#include "can_communication.h"

#include <bitset>

//#include "hss-esp.hpp"
#include "hss-esp-expander.hpp"
#include "button_gpio.h"
#include "iot_button.h"
#include "esp_sleep.h"

static const char *TAG = "main";

using namespace std;
using namespace std::chrono;
using namespace idf;
using namespace idf::esp_timer;

using namespace hss;

const auto test_sleep_time = seconds{3};
const auto ms50 = milliseconds(50);
const auto sec2 = milliseconds(2000);


//#include <driver/i2c_master.h>

#define I2C_MASTER_SCL_IO           SCL_GPIO(21)      /*!< GPIO number used for I2C master clock */
#define I2C_MASTER_SDA_IO           SDA_GPIO(22)      /*!< GPIO number used for I2C master data  */

#define BUTTON_PIN 34
#define BUTTON_ACTIVE_LEVEL     0

static void button_event_cb(void *arg, void *data)
{
    ESP_LOGI(TAG, "BTN pressed");
    LedStripDriver *driver = (LedStripDriver*) data;
    for (auto led: driver->leds){
        led->toggle();
    }

}

class Buttons{
    public: 
    Buttons(LedStripDriver *led_driver){
        button_config_t btn_cfg = {0};
        button_gpio_config_t gpio_cfg = {
            .gpio_num = BUTTON_PIN,
            .active_level = BUTTON_ACTIVE_LEVEL,
            .enable_power_save = false,
            .disable_pull = true,
        };
    
        button_handle_t btn;
        esp_err_t ret = iot_button_new_gpio_device(&btn_cfg, &gpio_cfg, &btn);
        assert(ret == ESP_OK);
    
        ret = iot_button_register_cb(btn, BUTTON_PRESS_DOWN, NULL, button_event_cb, led_driver);
    }

    private:
    vector<button_handle_t> buttons;
};

void adc_init(adc_oneshot_unit_handle_t *handle, adc_channel_t adc_channel)
{
    // ADC2 CH2

    adc_oneshot_unit_init_cfg_t init_config1 = {
        .unit_id = ADC_UNIT_2,
        .ulp_mode = ADC_ULP_MODE_DISABLE,
    };
    ESP_ERROR_CHECK(adc_oneshot_new_unit(&init_config1, handle));

    //-------------ADC1 Config---------------//
    adc_oneshot_chan_cfg_t config = {
        .atten = ADC_ATTEN_DB_12,
        .bitwidth = ADC_BITWIDTH_DEFAULT,
    };
    ESP_ERROR_CHECK(adc_oneshot_config_channel(*handle, adc_channel, &config));
}


void test_rmt_multi_ch(){

    const GPIO_Output led_en(GPIONum(32));
    led_en.set_high();

}



void test_water_sensor(){
    const GPIOInput pin(GPIONum(34));
    pin.set_pull_mode(GPIOPullMode::PULLDOWN());

    while(1){
        cout << "pin read: " << (int)pin.get_level() << endl;
        this_thread::sleep_for(std::chrono::seconds(2));
    }
}

void test_mux()
{
    shared_ptr<I2CMaster> master(new I2CMaster(I2CNumber::I2C0(),
                I2C_MASTER_SCL_IO,
                I2C_MASTER_SDA_IO,
                Frequency(400000)));
    ESP_LOGI(TAG, "I2C initialized successfully");
    esp_io_expander_handle_t io_expander = NULL;
    esp_err_t status;
    
    status = esp_io_expander_new_i2c_tca95xx_16bit(I2C_NUM_0, ESP_IO_EXPANDER_I2C_TCA9555_ADDRESS_010, &io_expander);
    //esp_io_expander_reset(io_expander);
    if(status != ESP_OK)
    {
        ESP_LOGE(TAG, "Failed to initialize tca expander");
        return;
    }

    Cd74HCMux mux( io_expander, IO_EXPANDER_PIN_NUM_0, IO_EXPANDER_PIN_NUM_1, IO_EXPANDER_PIN_NUM_2, IO_EXPANDER_PIN_NUM_3);   

    esp_io_expander_pin_num_t pin = IO_EXPANDER_PIN_NUM_6;

    ESP_ERROR_CHECK(esp_io_expander_set_dir(io_expander, pin, IO_EXPANDER_INPUT));


    while(1)
    {
        uint32_t pin_lvl = 99;
        ESP_ERROR_CHECK(esp_io_expander_get_level(io_expander, pin, &pin_lvl));

        std::bitset<32> x(pin_lvl);

        //mux.enable_channel(i); 
        cout << x << endl;     
        ESP_LOGI(TAG, "ch5: %d", int(x[6]));
        this_thread::sleep_for(chrono::seconds(2)); 

    }
}

void hss_test_thread(){

    shared_ptr<I2CMaster> master(new I2CMaster(I2CNumber::I2C0(),
                I2C_MASTER_SCL_IO,
                I2C_MASTER_SDA_IO,
                Frequency(400000)));
    esp_io_expander_handle_t io_expander = NULL;
    esp_err_t status;
    
    status = esp_io_expander_new_i2c_tca95xx_16bit(I2C_NUM_0, ESP_IO_EXPANDER_I2C_TCA9555_ADDRESS_010, &io_expander);
    //esp_io_expander_reset(io_expander);
    if(status != ESP_OK)
    {
        ESP_LOGE(TAG, "Failed to initialize tca expander");
        return;
    }
     
    adc_oneshot_unit_handle_t adc_handle;
    adc_channel_t adc_channel = ADC_CHANNEL_2;
    adc_init(&adc_handle, adc_channel);

    Cd74HCMux mux( io_expander, IO_EXPANDER_PIN_NUM_0, IO_EXPANDER_PIN_NUM_1, IO_EXPANDER_PIN_NUM_2, IO_EXPANDER_PIN_NUM_3);   

    //TODO put this into #DEFINEs
    uint8_t ch1_diag_mux_pin = 8;
    uint8_t ch5_diag_mux_pin = 12;

    HssEspExpander hss1(io_expander, IO_EXPANDER_PIN_NUM_10, IO_EXPANDER_PIN_NUM_15, 
        &mux, ch1_diag_mux_pin, adc_handle, adc_channel, 
        &hss::BTS7006);
    HssEspExpander hss5(io_expander, IO_EXPANDER_PIN_NUM_6, IO_EXPANDER_PIN_NUM_11, 
        &mux, ch5_diag_mux_pin, adc_handle, adc_channel,
        &hss::BTS7006);


    hss1.init();
    hss5.init();
    hss1.enable();
    hss5.enable();

    hss1.enableDiag();
    hss5.enableDiag();

    hss1.disable();
    this_thread::sleep_for(chrono::milliseconds(500));  
    hss1.enable();

    int adc_raw = 0;
    int voltage = 0;
    bool state = 0;
    uint16_t r_sense = 1410;

    while(1)
    {
        float sense_current = hss5.readIs(r_sense);
        int diag_status = hss5.diagRead(sense_current);
        ESP_LOGI(TAG, "sensed current: %f", sense_current);
        ESP_LOGI(TAG, "HSS5 diag msg: %d", diag_status);

        hss5.print_diag(diag_status);
        this_thread::sleep_for(test_sleep_time);  


        sense_current = hss1.readIs(r_sense);
        diag_status = hss1.diagRead(sense_current);
        ESP_LOGI(TAG, "sensed current: %f", sense_current);
        ESP_LOGI(TAG, "HSS1 diag msg: %d", diag_status);

        hss1.print_diag(diag_status);
        this_thread::sleep_for(test_sleep_time);  

        // hss5.disable();
        // this_thread::sleep_for(chrono::milliseconds(500));  
        // hss5.enable();

    }
}

const auto sleep_time = seconds
{
    10
};


void print_thread_info(const char *extra = nullptr)
{
    std::stringstream ss;
    if (extra) {
        ss << extra;
    }
    ss << "Core id: " << xPortGetCoreID()
       << ", prio: " << uxTaskPriorityGet(nullptr)
       << ", minimum free stack: " << uxTaskGetStackHighWaterMark(nullptr) << " bytes.";
    ESP_LOGI(pcTaskGetName(nullptr), "%s", ss.str().c_str());
}

void thread_func_inherited()
{
    while (true) {
        //print_thread_info("This is the INHERITING thread with the same parameters as our parent, including name. ");
        std::this_thread::sleep_for(sleep_time);
    }
}

void spawn_another_thread()
{
    // Create a new thread, it will inherit our configuration
    std::thread inherits(thread_func_inherited);

    while (true) {
        print_thread_info();
        std::this_thread::sleep_for(sleep_time);
    }
}

void thread_func_any_core()
{
    while (true) {
        //print_thread_info("This thread (with the default name) may run on any core.");
        std::this_thread::sleep_for(sleep_time);
    }
}

void spawn_temp_thread(){

    TempSensorDriver temp_sensors(GPIO_NUM_33);

    ESP_LOGI(TAG, "Setting up timer to read temperature update every 1000 ms\n");
    function<void()> temp_update = [&]() { temp_sensors.read();};
    ESPTimer timer(temp_update);
    timer.start_periodic(chrono::milliseconds(5000));
}

esp_pthread_cfg_t create_config(const char *name, int core_id, int stack, int prio)
{
    auto cfg = esp_pthread_get_default_config();
    cfg.thread_name = name;
    cfg.pin_to_core = core_id;
    cfg.stack_size = stack;
    cfg.prio = prio;
    return cfg;
}

void old_main(){


    test_rmt_multi_ch();

    // this_thread::sleep_for(std::chrono::seconds(4));



    // Create a thread on core 0 that spawns another thread, they will both have the same name etc.
    auto cfg = create_config("Thread Temp Sens", 0, 3 * 1024, 5);
    cfg.inherit_cfg = true;
    esp_pthread_set_cfg(&cfg);
    std::thread thread_1(spawn_temp_thread);


  // Analog UI
  ButtonConfig_t btn_heater = {GPIO_NUM_5, "heater"};
  ButtonConfig_t btn_mains = {GPIO_NUM_18, "mains"};
  ButtonConfig_t btn_water = {GPIO_NUM_19, "water"};
  AnalogUiButtonsConfig_t buttons_config = {btn_heater, btn_mains, btn_water};

  AnalogUiConfig_t analog_ui_config = {
      .update_frequency = 20, 
      .led_strip_gpio=GPIO_NUM_15,
      .buttons_config = buttons_config,
      .water_lvl_leds = {0,1,2,3},
      .normal_leds = vector<uint16_t>(175)
  };
  iota(analog_ui_config.normal_leds.begin(), analog_ui_config.normal_leds.end(), 4);
  /*
  TEST BEGIN
  */
  AnalogUI ui(analog_ui_config);

  ui.init_hardware();


  
  // Create a thread on core 1.
  cfg = create_config("Buttons Thread", 1, 3 * 1024, 5);
  esp_pthread_set_cfg(&cfg);
  Buttons btns({&ui.led_driver});

  //std::thread thread_2(button_init);
  //ui.loop();



  for(auto led: ui.led_driver.leds){
    led->set_brightness(100);
    led->set_color(Color::white());
    led->on();
    //this_thread::sleep_for(chrono::milliseconds(20));
  }
  ESP_LOGI(TAG, "Setting up timer to trigger UI update every 10ms\n");
  function<void()> ui_update = [&]() { ui.update();};
  idf::esp_timer::ESPTimer ui_timer(ui_update);
  ui_timer.start_periodic(chrono::milliseconds(100));
  //ui.test_fun();   
//   for(auto i=0; i<5; i++){
//     auto led = ui.led_driver.leds[i];
//     ESP_LOGI(TAG, "LED setup");
//     led->set_brightness(10);
//     led->set_color(Color::red());
//     led->flash(2000);
//     this_thread::sleep_for(std::chrono::milliseconds(100));
//   }  

    // Let the main task do something too
    while (true) {
        cout << ".\n";
        std::this_thread::sleep_for(sleep_time);
    }

}

extern "C" void app_main(void)
{

    init_can();

    WaterSensor ws();
        /*
    1. assign gpios to peripherials
    2. start ccu thread
        -water sensor timer
        -temp sensors timer
        -analog_ui timer (optional)
        -rmt lightning timer (update LEDs every xx ms)
        -digital switching control timer
    3. start CAN thread
    4. start BLE thread
    
  Possible events:
    generated by
        digital_switching
            -short circuit
            -overcurrent
        analog_ui

    
    
    */



}

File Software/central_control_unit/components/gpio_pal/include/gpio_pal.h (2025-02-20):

#include <iostream>

enum Error_t
{
    OK                   =  0,   /**< No error */
    INTF_ERROR           = -1,   /**< Interface error */
    CONF_ERROR           = -2,   /**< Configuration error */
    READ_ERROR           = -3,   /**< Read error */
    WRITE_ERROR          = -4,   /**< Write error */
    NULLPTR_ERROR        = -5,   /**< Null pointer error */
    INVALID_CH_ERROR     = -6,   /**< Invalid channel error */
    UNSUPPORTED_OP_ERROR = -7,   /**< Invalid channel error */
    INIT_ERROR           = -8    /**< Not initialized */
};
/**
 * @class   GPIOPAL
 * @brief   GPIO abstract API
 */
class GPIOPAL
{
    public:

        /**
         * @brief   Interrupt event
         */
        enum IntEvent_t
        {
            INT_FALLING_EDGE   = 0,     /**< Interrupt on falling edge */
            INT_RISING_EDGE    = 1,     /**< Interrupt on rising edge */
        };

        /**
         * @brief   Voltage level
         */
        enum VLevel_t
        {
            GPIO_LOW   = 0,        /**< Level low */
            GPIO_HIGH  = 1         /**< Level high */
        };

        /**
         * @brief   Voltage logic
         */
        enum VLogic_t
        {
            NEGATIVE = 1,       /**< Negative logic. 0 on voltage level high, 1 on voltage low */
            POSITIVE = 2,       /**< Positive logic. 1 on voltage level high, 0 on voltage low */
        };

        /**
         * @brief       Initializes the GPIO
         * @return High-side switch error code 
         * @retval      OK          If success
         * @retval      INIT_ERROR  If initialization error
         */
        virtual Error_t        init        () = 0;

        /**
             * @brief       Deinitializes the GPIO
             * @return High-side switch error code 
             * @retval      OK          If success
             * @retval      INIT_ERROR  If deinitialization error
         */
        virtual Error_t       deinit      () = 0;

        /**
         * @brief       Reads the GPIO voltage level
         * @return      VLevel_t
         * @retval      GPIO_LOW    If voltage low
         * @retval      GPIO_HIGH   If voltage high
         */
        virtual VLevel_t       read        () = 0;

        /**
         * @brief       Writes the GPIO output voltage level
         * @param[in]   level  Voltage level
         * @return High-side switch error code 
         * @retval      OK              If success
         * @retval      WRITE_ERROR     If write error
         */
        virtual Error_t        write       (VLevel_t level) = 0;

        /**
         * @brief       Enables the GPIO output according to the GPIO logic
         *              - Low if negative
         *              - High if positive
         * @return High-side switch error code 
         * @retval      OK              If success
         * @retval      WRITE_ERROR     If write error
         */
        virtual Error_t        enable      () = 0;

        /**
         * @brief       Disables the GPIO output according to the GPIO logic
         *              - Low if positive
         *              - High if negative
         * @return High-side switch error code 
         * @retval      OK              If success
         * @retval      WRITE_ERROR     If write error
         */
        virtual Error_t        disable     () = 0;

};

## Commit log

2024-09-15 initial basic structure with BTS driver
2024-11-17 bulk update. UI working nice on 7inch screen under Linux (RPI) framebuffer
2024-11-24 ina first try with rp pico. both, read and write works fine though. some functions not
    [bmp280_i2c.fzz]
2024-12-08 esp-crow-panel-7 works
    [CrowPanel ESP32 Display-7.0-inch-V3.0-20240420.brd, CrowPanel ESP32 Display-7.0-inch-V3.0-20240420.sch]
2024-12-15 much cleaner files structure. more observers and ESP-specific stuff separation
    [partitions.csv]
2024-12-20 progress made on electronics part
    [centra_control_unit.kicad_sch, electronics.kicad_pcb, electronics.kicad_sch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]
2024-12-30 from Legion
    [CrowPanel ESP32 Display-7.0-inch-V3.0-20240420.brd, CrowPanel ESP32 Display-7.0-inch-V3.0-20240420.sch, centra_control_unit.kicad_sch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]
2025-01-01 hss GPIO implemented, compiling fine
    [centra_control_unit.kicad_sch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]
2025-01-19 hss_test_thread and DC/DC converter blowup after short-circuit test
    [hss-esp-expander.cpp, hss-esp.cpp, hss-pal-adc-esp-expander.cpp]
2025-01-20 porady od MichalaG
    [centra_control_unit.kicad_sch, electronics.kicad_pcb, high_power.kicad_sch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]
2025-01-23 lisbon flight changes
    [centra_control_unit.kicad_sch, electronics.kicad_pcb, high_power.kicad_sch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]
2025-01-29 flight back. different layout. start analog ui
    [230VAC.kicad_sch, CAN.kicad_sch, analog_ui.kicad_sch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]
2025-01-31 no tracks, but placement looks good
    [230VAC.kicad_sch, centra_control_unit.kicad_sch, dc_dc_conversion.kicad_sch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]
2025-02-03 nerd weekend update
    [blown_fuse_detection.kicad_sch, digital_switching.kicad_sch, electronics.kicad_pcb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]
2025-02-08 added analog_ui based on led_strip. flashin, timers, colors and brightness works. all in c++ sty;e
2025-02-09 basic temp sensor on RMT DS18B20. analogUI stopped working...
    [230VAC.kicad_sch, CAN.kicad_sch, analog_ui.kicad_sch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]
2025-02-24 project cleanup
    [CrowPanel ESP32 Display-7.0-inch-V3.0-20240420.brd, CrowPanel ESP32 Display-7.0-inch-V3.0-20240420.sch, bmp280_i2c.fzz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]
2025-02-25 start to create BOM and finalising symbol fields
    [230VAC.kicad_sch, CAN.kicad_sch, additional-esp-conn.kicad_sch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]
2025-02-26 progres on layouting
    [230VAC.kicad_sch, CAN.kicad_sch, analog_ui.kicad_sch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]
2025-03-02 layouting progress. some 3d models upload
    [230VAC.kicad_sch, 3p-10-conn v2.step, ATO-fuse-holder v0.step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]

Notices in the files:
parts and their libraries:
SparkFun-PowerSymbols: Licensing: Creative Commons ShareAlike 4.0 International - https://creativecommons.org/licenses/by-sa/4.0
